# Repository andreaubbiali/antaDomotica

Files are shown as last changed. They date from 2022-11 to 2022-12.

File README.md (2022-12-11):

# Anta domotica

Il progetto consiste nel progettare un'anta domotica la quale si apre/chiude in base alla presenza di luce diretta oppure tramite input esterni (bottoni o messaggi di rete). 
L'idea di base nasce dal fatto che il mio ufficio al mattino rimane all'ombra mentre, negli orari pomeridiani, il sole punta diretto all'interno rendendomi difficoltoso il lavoro da pc.

L'apertura o chiusura può essere comandata in due modi:
- <b>automatico</b>: lo stato dell'anta viene deciso automaticamente in base alla presenza di luce diretta (valutata dalla fotoresistenza) ed in base all'orario corrente. Quest ultimo può servire nel caso in cui l'utente voglia che da un certo orario serale fino ad un certo orario alla mattina, le ante rimangano chiuse.

- <b>manuale</b>: lo stato dell'anta può essere modificato tramite la pressione dei bottoni fisici collegati direttamente alla board oppure tramite l'invio di messaggi con il protocollo mqtt.

Ogni qualvolta l'anta si muove, viene attivato (in base a se si sta aprendo o chiudendo) il rispettivo sensore di prossimità, necessario per controllare che non ci sia alcun ostacolo nel raggio di movimento. Qualora il sensore rilevasse un ostacolo il movimento verrà bloccato. Questo tipo di controllo non avviene nel primo movimento di assestamento dell'anta, attenzione quindi che l'intero raggio d'azione sia libero per questo istante.

Per rilevare l'arrivo dell'anta a destinazione, sono stati posti due finecorsa (uno per l'apertura ed uno per la chiusura).

È inoltre presente un sensore di temperatura ed umidità, utilizzato per raffinare il calcolo della distanza calcolato dai sensori di prossimità.

## Messaggi mqtt
Di seguito i messaggi mqtt utilizzati (prefisso generale `antaDomotica/aubbiali`):

### Subscription

- sensor
    ```
    /doorMovement
    payload:
        - DS_STOP -> stop distance sensor
        - ACTIVATE_DS_CLOSE -> activate distance sensor close
        - ACTIVATE_DS_OPEN -> activate distance sensor open
    ```

- movement
    ```
    /moveDoor
    payload:
        - "close" -> close the door (if manual)
        - "open" -> open the door (if manual)

    /setManual
    payload:
        - "1" -> set manual true
        - "0" -> set manual false

    /distanceSensor
    payload:
        - DS_ACTIVATED -> received distance sensor activated

    /setCloseTime
    payload:
        - "time" -> set the close time (hh)

    /setOpenTime
    payload:
        - "time" -> set the open time (hh)
    ```

### Publish

- sensor
    ```
    /distanceSensor
    payload:
        - DS_ACTIVATED -> send signal distance sensor activated

    /temperature
    payload:
        - string -> temperature value

    /humidity
    payload:
        - string -> temperature value
    ```

- movement
    ```
    /doorStatus
    payload:
        - "close" -> the door is closed
        - "open" -> the door is open

    /doorMovement
    payload:
        - "close" -> send the close signal
        - "open" -> send the open signal

    /closeTime
    payload:
        - "hours" -> send the close hours

    /openTime
    payload:
        - "hours" -> send the open hours

    /isManual
    payload:
        - bool -> send is manual value

    /photoResistenceResp
    payload:
        - string -> send photoresistence response 

    ```

## Circuito

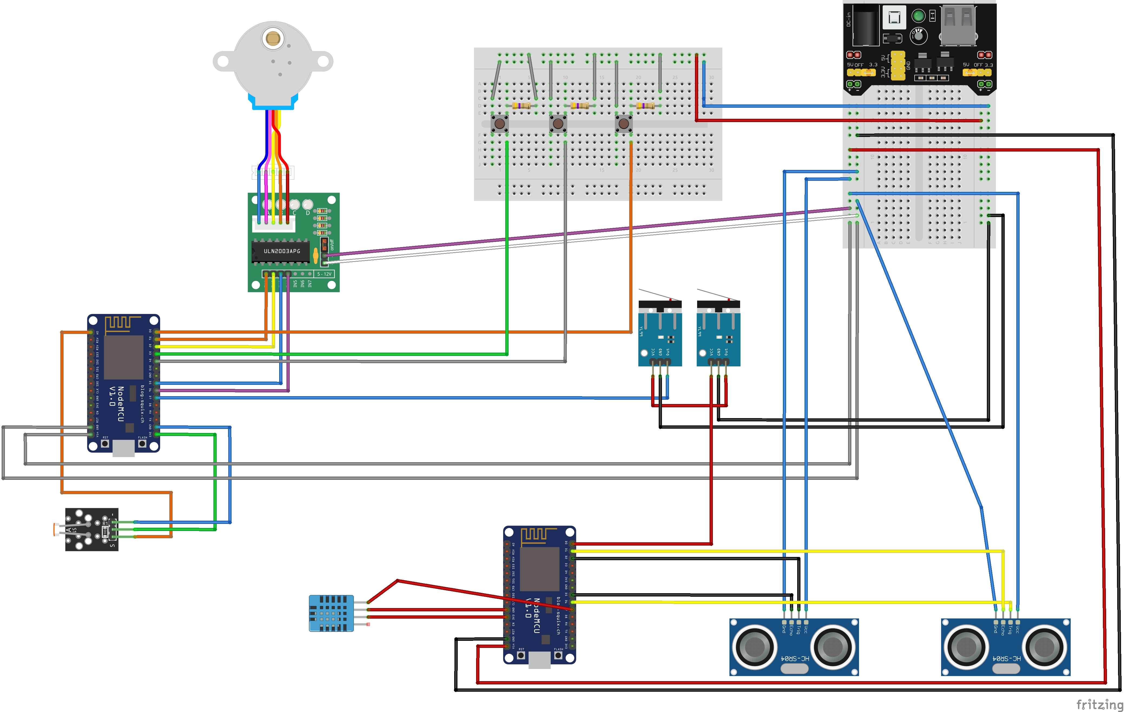
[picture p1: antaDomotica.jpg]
Fritzing circuit


## Valori di default

Se non settati dalle `constant.h` l'anta si chiuderà alle 22 e si aprirà alle 6 di defaul

## Logica automatica:

L'obiettivo è chiudere l'anta a prescindere la sera e riaprirla (qualora non ci sia il sole diretto) la mattina:

photoresistence -> close        time -> open   = close\
photoresistence -> open         time -> close  = close\
photoresistence -> open         time -> open   = open\
photoresistence -> close        time -> close  = close

<b> !ATTENTION! </b>
At the moment, for implementation behaviour, close time must be > of the open time.
So for example
```
open-time: 06:00
close-time: 23:00
```

## Photoes


 
https://user-images.githubusercontent.com/44111217/206721258-0ae9b58c-8fa4-4f94-9945-c57a270a05e9.mp4

https://user-images.githubusercontent.com/44111217/206721718-c84176ce-9c02-403d-8d9d-294fac7fad00.MP4

# TODO

- utilizzare task scheduler invece di loop nelle varie funzioni del codice
- utilizzare una sola board
- sistemare il circuito in modo tale da sapere se il blocco del movimento dell'anta è causato da switch open, switch close o ostacolo trovato. Non utilizzare più quindi la connessione in serie dei componenti board-switch1-switch2.
- sistemare le funzioni che hanno dei timeout interni (per esempio la funzione pulseIn, se non erro, aspetta il ritorno del segnale per un tot di tempo, ti tiene ferma la computazione per quel tot di tempo).

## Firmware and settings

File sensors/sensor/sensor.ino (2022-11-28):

#include <DHT.h>
#include "EspMQTTClient.h"
#include "/home/aubbiali/universita/sisEmbedded/WifiConfig.h"
#include "/home/aubbiali/universita/sisEmbedded/antaDomotica/constant.h"

#define DHTPIN D7  // Digital pin connected to the DHT sensor
#define trigPinClose D2
#define echoPinClose D5

#define trigPinOpen D6
#define echoPinOpen D1

#define DHTTYPE DHT11

const int obstaclePinSignal = D0;
float temperature = 1.0;
float duration, distance;
bool checkSensor;
uint trigP, echoP;

DHT dht(DHTPIN, DHTTYPE);

EspMQTTClient mqttClient(
  WIFI_SSID,
  WIFI_PSW,
  "test.mosquitto.org",
  "distanceSensorClient",
  1883
);

void setup() {
  Serial.begin(115200);
  pinMode(trigPinClose, OUTPUT);
  pinMode(echoPinClose, INPUT);
  pinMode(trigPinOpen, OUTPUT);
  pinMode(echoPinOpen, INPUT);
  pinMode(obstaclePinSignal, OUTPUT); 

  checkSensor = false;

  digitalWrite(obstaclePinSignal, HIGH);
  dht.begin();

  while(!mqttClient.isConnected()){
    mqttClient.loop();
    delay(100);
  }
  
  readTemperature();
}

void loop() {

  if (checkSensor) {
    distanceSensor();
  }
    
  mqttClient.loop();
  delay(150);    
}

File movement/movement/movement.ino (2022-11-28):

#include <ESP8266WiFi.h>
#include <NTPClient.h>
#include <WiFiUdp.h>
#include <AccelStepper.h>
#include "EspMQTTClient.h"
#include "/home/aubbiali/universita/sisEmbedded/WifiConfig.h"
#include "/home/aubbiali/universita/sisEmbedded/antaDomotica/constant.h"

// ULN2003 Motor Driver Pins
#define IN1 D1
#define IN2 D2
#define IN3 D5
#define IN4 D6
AccelStepper stepper(AccelStepper::HALF4WIRE, IN1, IN3, IN2, IN4);

const uint limitSwitchOrObstacle = D7;
const uint buttonClose = D0;
const uint buttonOpen = D4;
const uint manAutomButton = D3;

const uint stepsPerRevolution = 4096;  // change this to fit the number of steps per revolution
const uint maxTimerResponse = 4000;
const uint automaticReadMinutes = AUTOMATIC_READ_MINUTE;
const String CLOSE = "close";
const String OPEN = "open";

unsigned long lastDebounceTimeSwitch = 0;  // the last time the output pin was toggled
const unsigned long debounceDelay = 1500;    // the debounce time; increase if the output flickers

uint lastAutomaticaRead = millis();
bool rotation, isOpen, isManual, sensorResponse;

// MQTT CLIENT
EspMQTTClient mqttClient(
  WIFI_SSID,
  WIFI_PSW,
  "test.mosquitto.org",
  "movementClient",
  1883
);

// NTP CLIENT to get time
WiFiUDP ntpUDP;
NTPClient timeClient(ntpUDP, "pool.ntp.org");

void setup() {
  Serial.begin(115200);
  
  // set stepper's speed and acceleration
  resetStepper();

  pinMode(buttonClose, INPUT);
  pinMode(buttonOpen, INPUT);

  // set interrupt
  pinMode(limitSwitchOrObstacle, INPUT);
  attachInterrupt(digitalPinToInterrupt(limitSwitchOrObstacle), limitSwitch, FALLING);
  pinMode(manAutomButton, INPUT);
  attachInterrupt(digitalPinToInterrupt(manAutomButton), manAutInterrupt, FALLING);
  
  while(!mqttClient.isConnected()){
    mqttClient.loop();
    delay(500);
  }

  setupNTP();

  initialDoorSetup();
  setIsManual(true);
}

void loop() {

  if (isManual) {
    if (digitalRead(buttonClose) == LOW) {
      closeDoor();
    } else if (digitalRead(buttonOpen) == LOW) {
      openDoor();
    }

  } else {
    
    if (millis() - lastAutomaticaRead > (automaticReadMinutes*60000)) {
      lastAutomaticaRead = millis();
      
      // get the movement to do based on time
      String respTime = movementOnTime();

      // read photoresistence
      String respPhotoRes = readPhotoresistence();

      moveDoorAutomaticLogic(respTime, respPhotoRes);
    }

  }

  mqttClient.loop();

  delay(150);
}

/**
* The purpose is that if I have decided to close the door it must remain closed (usually during the night) while if is automatic and I said to open it, 
* if the photresistence decide to close it, the door should be closed.
* 
* photoresistence -> close        time -> open   = close
* photoresistence -> open         time -> close  = close
* photoresistence -> open         time -> open   = open
* photoresistence -> close        time -> close  = close
*/
void moveDoorAutomaticLogic(String respTime, String respPhotoRes){
  if (respTime == respPhotoRes) {
    if (respTime == CLOSE){
      closeDoor();
    } else if (respTime == OPEN) {
      openDoor();
    }
  }

  if (respPhotoRes == CLOSE && respTime == OPEN){
    closeDoor();
  }

  if (respPhotoRes == OPEN && respTime == CLOSE) {
    closeDoor();
  }
}

/**
* Set the is manual value.
* isManual = true -> are used buttons to move the door.
* isManual = false -> are used time and photoresistence to move the door.
*/
void setIsManual(bool value){
  isManual = value;
  sendUpdateIsManual();
}

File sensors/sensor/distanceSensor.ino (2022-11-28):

const int minDistanceObstacle = 3;
int countPossibleObstacle;
const int maximumPossibleObstacle = 3;

/**
* Populate (and send to mqtt) the temperature field with the new temperature if is present otherwise mantain the old temperature.
* 
*/
void readTemperature(){
  float temp = dht.readTemperature();
  if (!isnan(temp)) {
    temperature = temp;
    sendTemperature();
  }

}

/**
* Calc of speed of sound
*/ 
float calcSpeedOfSound() {
  readTemperature();

  return 331.3 + 0.606 * temperature;
}

/**
* Start distance sensor to check if exist an obstacle.
*/
void distanceSensor(){

  float speedOfSound = calcSpeedOfSound();
  countPossibleObstacle = 0;
  sendSensorStartMessage();

  while(checkSensor){
    digitalWrite(trigP, LOW);
    delayMicroseconds(2);
    digitalWrite(trigP, HIGH);
    delayMicroseconds(10);
    digitalWrite(trigP, LOW);

    duration = pulseIn(echoP, HIGH);
    float distance = (duration / 20000.0) * speedOfSound;

    if (distance > 1 && distance < minDistanceObstacle) {
      countPossibleObstacle += 1;
      checkSensor = !isInterruptSended(countPossibleObstacle);
    }

    mqttClient.loop();
    delay(100);
  }
}

/**
* Send interrupt (to stop the movement) if count is bigger than the maximum possible obstacle counter
*/
bool isInterruptSended(int count) {

  if (count >= maximumPossibleObstacle) {
    digitalWrite(obstaclePinSignal, LOW);
    delay(500);
    digitalWrite(obstaclePinSignal, HIGH); 
    return true;                 
  }

  return false;
}

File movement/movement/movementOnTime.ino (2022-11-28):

/**
* Movement based on the time specified
*/
int closeHour, openHour = 0;

void setupNTP(){
  WiFi.begin(WIFI_SSID, WIFI_PSW);
  while (WiFi.status() != WL_CONNECTED) {
    delay(500);
  }
  timeClient.begin();
  timeClient.setTimeOffset(3600);

  // set default close time
  String time = CLOSE_TIME;
  if(!isCorrectTime(time)){
    time = "22";
  }
  setCloseTime(time);

  // set default open time
  time = OPEN_TIME;
  if(!isCorrectTime(time)){
    time = "06";
  }
  setOpenTime(time);
}

/**
* Return the status the door should be based on the time.
* If is in the interval from open to close -> open
*/
String movementOnTime() {
  timeClient.update();
  int currentHour = timeClient.getHours();

  if (currentHour >= openHour && currentHour < closeHour){
    return OPEN;     
  }

  return CLOSE;
}

/**
* Check if a time is in the correct format (is an integer number between 0 and 24)
*/
bool isCorrectTime(String time){

  uint hours = time.toInt();
  if ((hours == 0 && time != "0") || hours > 24){
    return false;    
  }
    
  return true;
}

// SETTER
/**
* Set close time checking its correctness with the open time
* !ATTENTION! call this method only after checking isCorrectTime
*/
void setCloseTime(String time){
  uint tmpHour = time.toInt();

  if (tmpHour < openHour) {
    return;
  }

  closeHour = tmpHour;
  sendUpdateCloseTime(closeHour);
}

/**
* Set open time checking its correctness with the close time
* !ATTENTION! call this method only after checking isCorrectTime
*/
void setOpenTime(String time){
  int tmpHour = time.toInt();

  if (tmpHour > closeHour){
    return;
  }
  
  openHour = tmpHour;
  sendUpdateOpenTime(openHour);
}

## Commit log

2022-11-01 Update sensor
2022-11-06 Added boards communication rxtx
2022-11-20 Switch from serial communication to mqtt
2022-11-24 added second sensor
2022-11-24 Changed some buttons pin
2022-11-24 moved button to interrupt
2022-11-24 fixed automatic door logic
    [movement.ino, photoResistence.ino]
2022-11-28 clean sensor code
2022-11-28 added circuit in readme
2022-11-28 Added fzz file
    [antaDomotica.fzz]
